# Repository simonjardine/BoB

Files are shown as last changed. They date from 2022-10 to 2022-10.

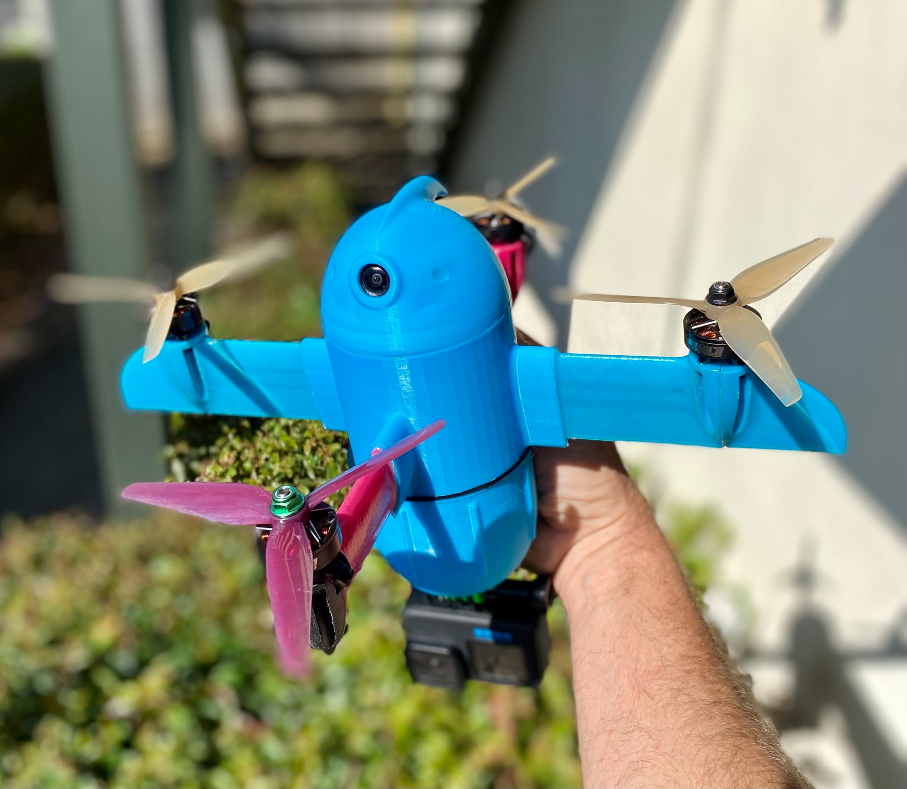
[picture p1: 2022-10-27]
bob.jpeg

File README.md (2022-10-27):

# BoB
Bob The Waterproof Drone
Hi, I'm BoB. I was born on the 10.10.2021 at 10.00am UTC

Simon Jardine is my maker, He built me and designed me to fly and even swim.
I'm called BoB because he said that I like to BoB, I also have a keel like a boat, so I always stay upright!!
Simon has been flying for 15 years, he thinks I'm the Worlds best Drone!!
So it must be true....

I am not the only waterproof Drone Simon has made, he made this one 10 years ago,
It was the very first waterproof Drone in The World.
https://www.youtube.com/watch?v=769Ppq-3Eaw&t=24s

How to build.. "BoB"

Apperently I'am a pleasure to build, everything slips in, wires will slide into the wings,
wings into fusealage, boom continues all the way to the motor mount.

You will need a 5mm boom to keep me rigid and strong for diving into the oceans.
The 5mm boom is a very tight fit, you will have to tap them carefully into the wings with a hammer, or sand them a little.
To keep me waterproof, use SikaSeal Aquarium Silicone Sealant, or something similar.
It's clear and easy to use, use a wet cloth to remove excess silicone.
Sand the parts first for a nice bond.

You'll also need superglue to connect my wing tips and motor mounts. Use medium CA and kicker for best adhesion!
There is a small hole in all of my motormounts, this was beacuse of my 5mm boom going all the way to my wingtips.
You will have to use silicone to fill these holes. 
Silicone also need to go into the wire section in the wings, both on the inside of the fusealage and end of wings.
Please don't super glue my Carbon boom, if you crash me, how will you repair me?

The STL files have 2 fuselage's, For a 20x20 FC and 30x30 FC.

The 30x30 fusealage also has another mounting hole for the Video Transmitter VTX, It was designed to use the TBS Transmitter.
Both holes use a 20x20 heatsink which are easyily purchased online.
Please note the larger ESC's will cope better with the heat and is highly recommended!!
The higher powered TX's also need a through hull fitting, becuase if I'm waterproof then things can get hot quickly.
It's also adviced to switch on temp within the OSD. You'll be able to keep an eye on my internal temperature.

Most importantly I fly as a PLUS not an X shape. So make sure in Betaflight to change me as a PLUS.
You will have to also adjust the YAW alignment. Make sure you check that I react correctly to your movements.

Enjoy BoB and please fly safely, Simon Jardine takes no responsibility for what you do with BoB.

HAPPY FLYING !!!!!!!!!!!

Simon and Bob :-)

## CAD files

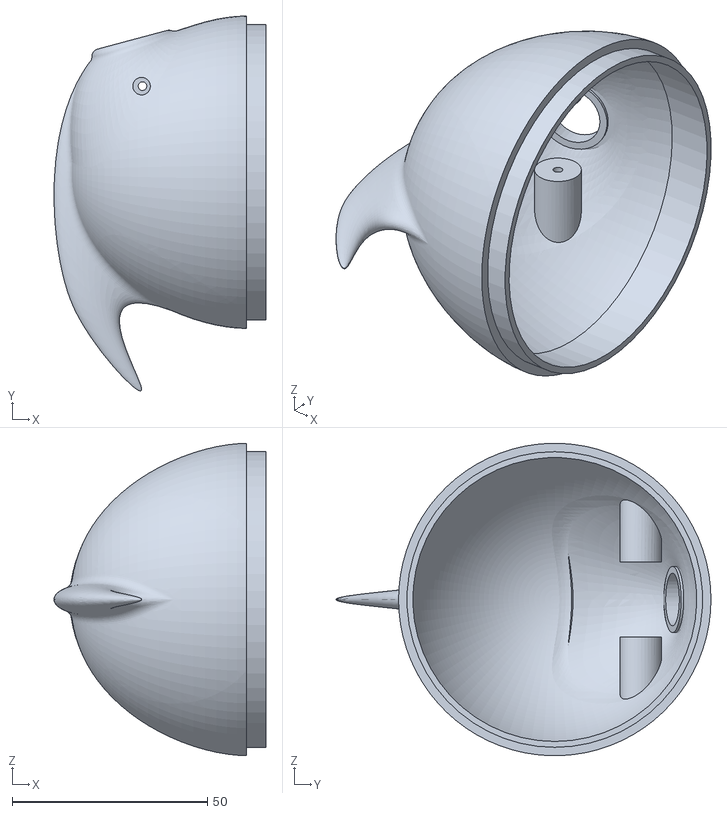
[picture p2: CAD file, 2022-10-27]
CanopyBottomparts/bobCanopy.STL
54.3 x 96.0 x 79.9

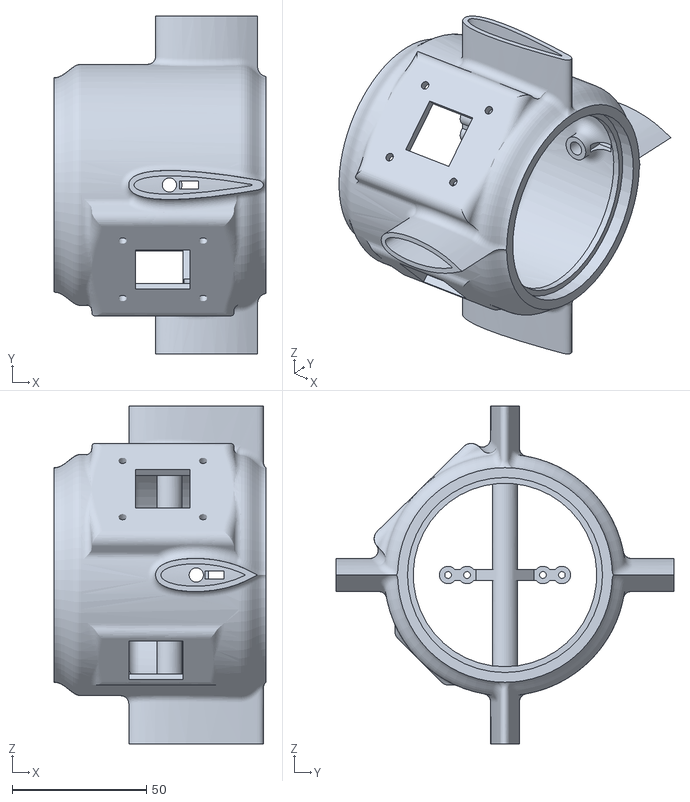
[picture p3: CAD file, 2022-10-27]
fuse30x30doubleheatsinks.STL
79.0 x 126.0 x 126.0

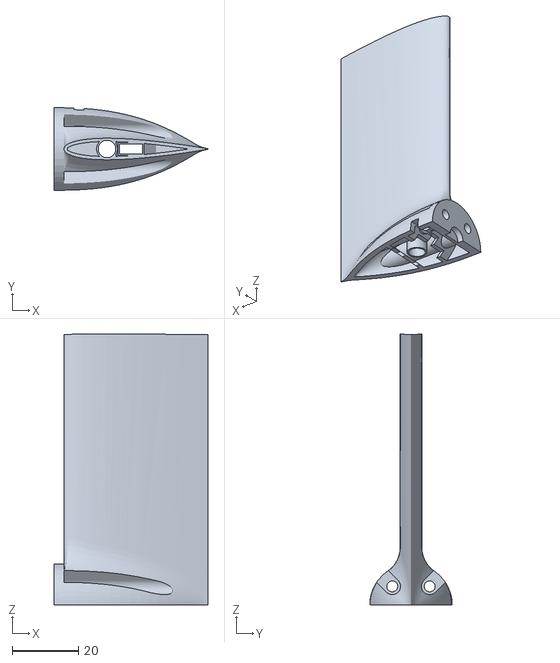
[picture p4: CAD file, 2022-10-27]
wingparts/leftwing.STL
46.6 x 25.0 x 82.1

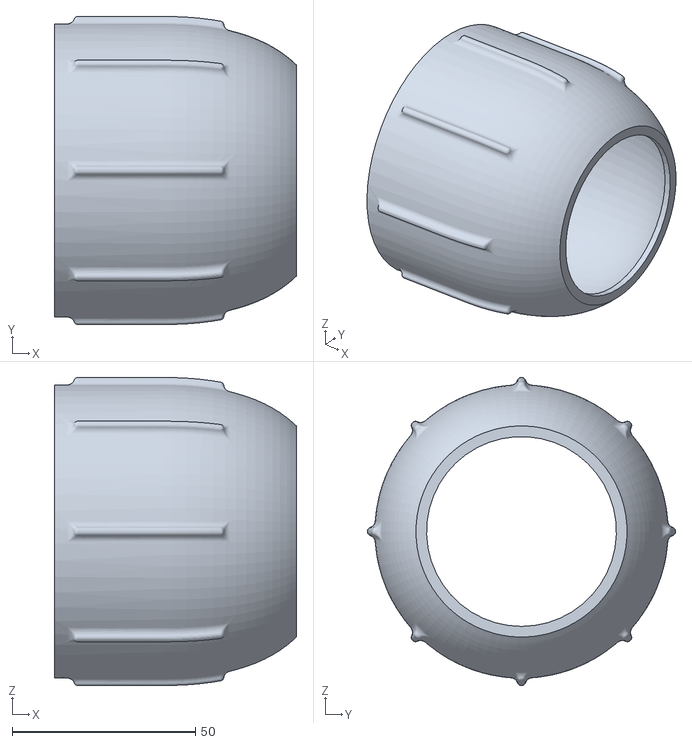
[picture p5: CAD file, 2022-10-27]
CanopyBottomparts/threadedbatteryholder.STL
66.0 x 84.0 x 84.0

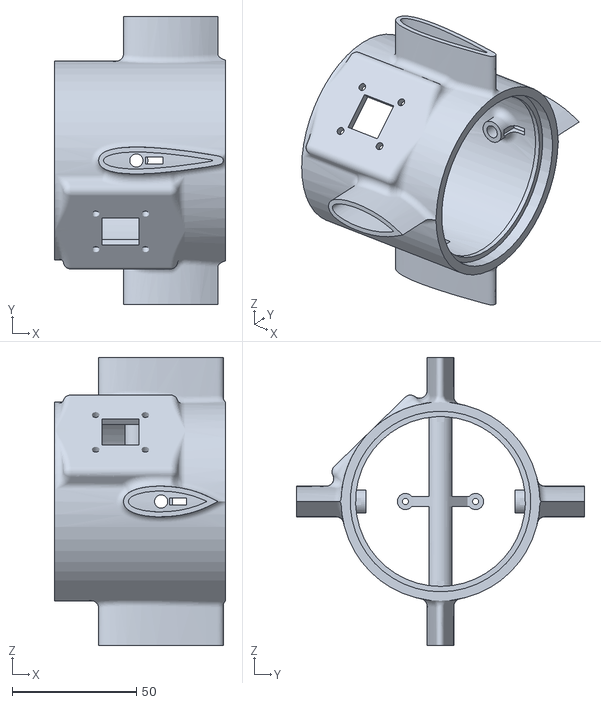
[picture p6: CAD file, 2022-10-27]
fuse20x20.STL
69.0 x 116.0 x 116.0

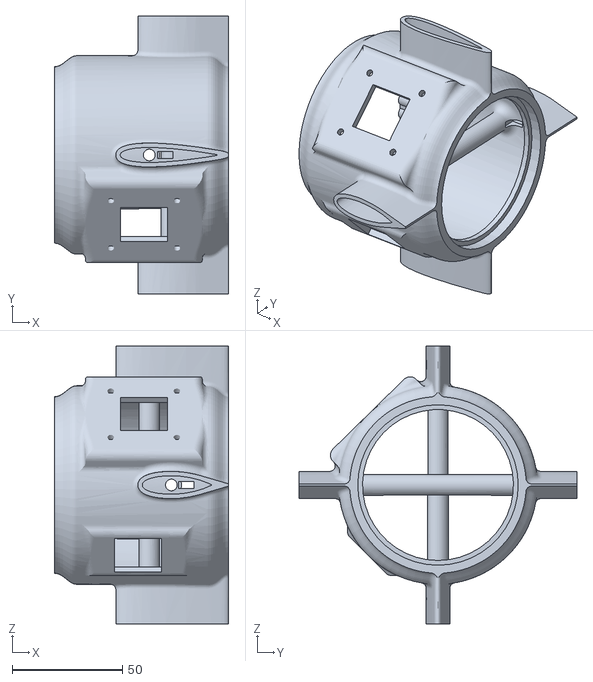
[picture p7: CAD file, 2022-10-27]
Mainfuselage/WP fuselage part2_2021.10.14.STL
79.0 x 126.0 x 126.0

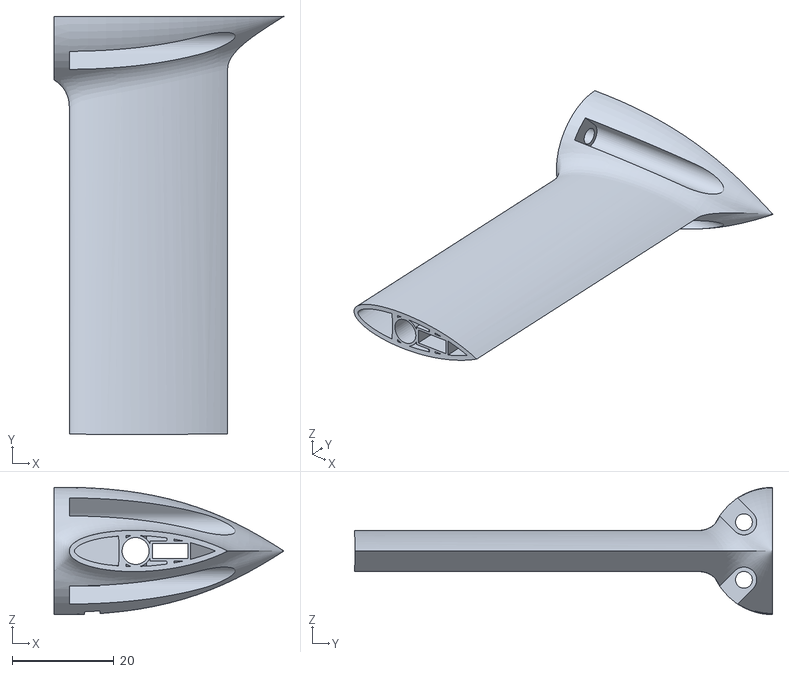
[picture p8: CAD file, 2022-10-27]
wingparts/bottomwing.STL
45.2 x 82.2 x 25.0

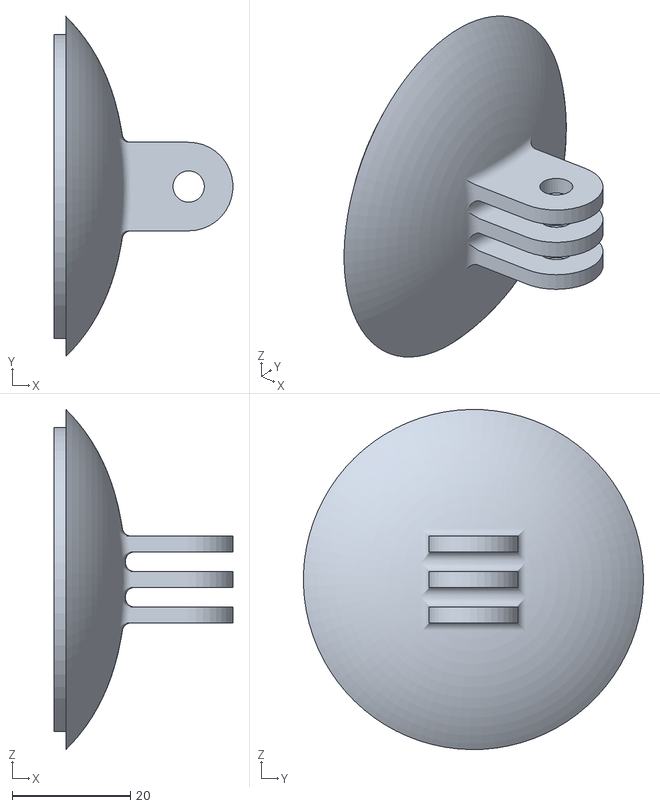
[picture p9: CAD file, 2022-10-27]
CanopyBottomparts/GoProbottom.STL
30.2 x 57.5 x 57.6

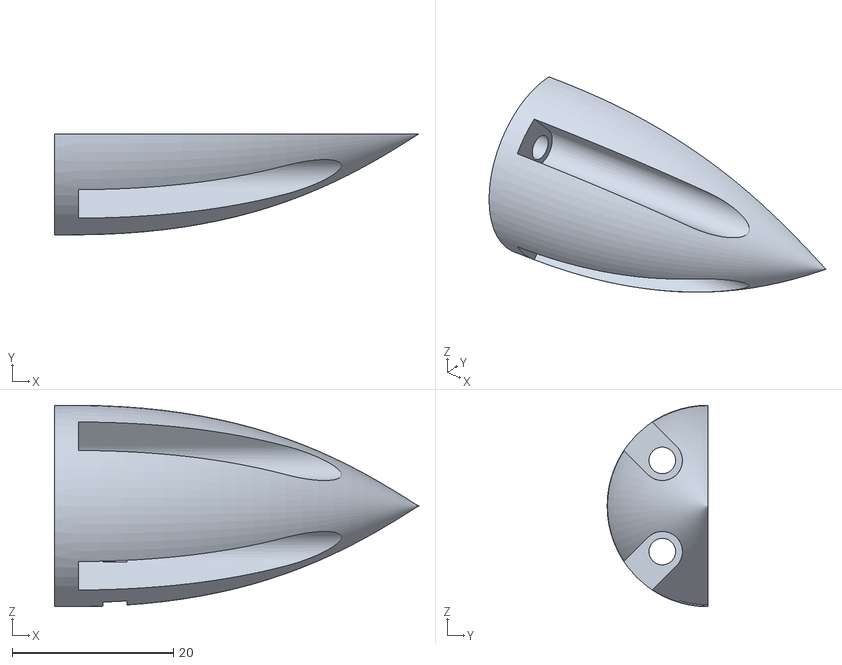
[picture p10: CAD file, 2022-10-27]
wingparts/topmotormount.STL
45.2 x 12.5 x 25.0

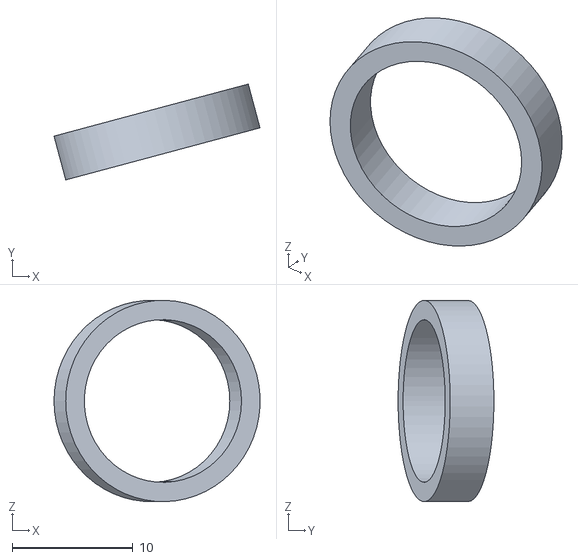
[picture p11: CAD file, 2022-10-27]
CanopyBottomparts/Ring for camera hole.STL
17.1 x 7.95 x 16.7

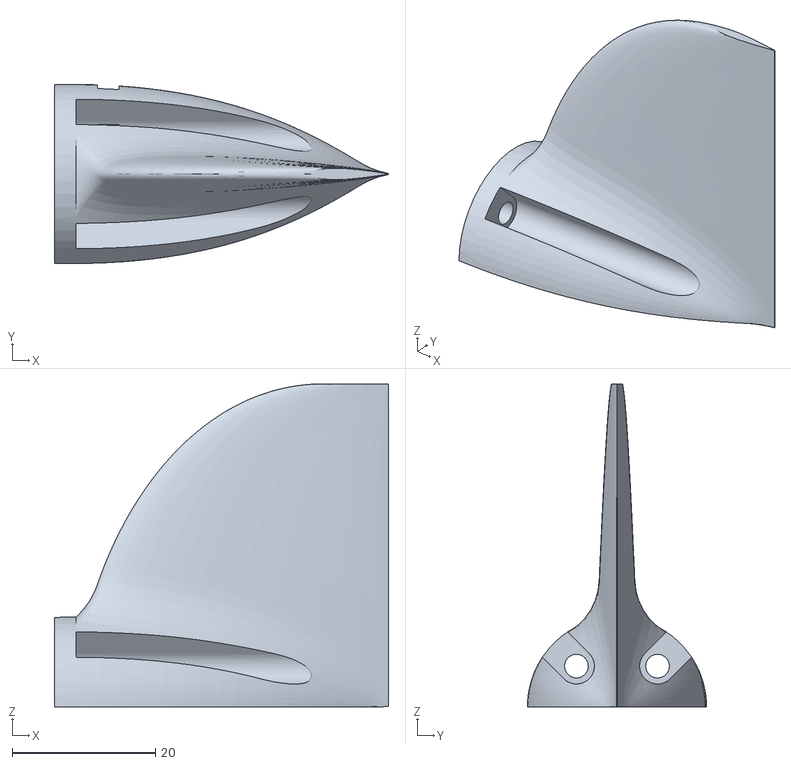
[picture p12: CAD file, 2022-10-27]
wingparts/rightwingtip.STL
46.6 x 25.0 x 45.0

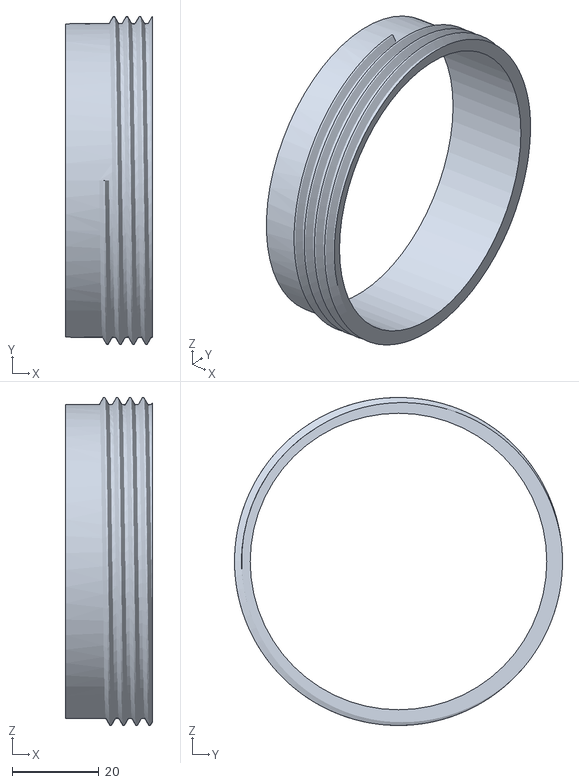
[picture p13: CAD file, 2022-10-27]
CanopyBottomparts/Lowerfusethread.STL
20.0 x 75.6 x 75.6

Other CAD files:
Mainfuselage/WP fuselage part2_larger ESC_with supports.STL
Mainfuselage/30x30fuselarger.STL
wingparts/rightwing.STL
wingparts/topwing.STL
wingparts/bottommotormount.STL
wingparts/leftwingtip.STL

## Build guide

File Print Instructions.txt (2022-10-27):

Printing....
I use an Ender 3 V2, but I also have the new FLsun Super Racer which is a Delta Printer (it's really amazing)

I am new to 3d Printing, so I won't be much use to you.
However these are the setting I used with great success.

I would use bright colours, Yellow, Orange, blue. 
I used PLA PLUS. You could also use any other materials, I've also used PLA/ 20%Carbon.
The GoPro mount must be printed in TPU slowly, (do not glue it until you have threaded the bottom on)
Or later when you go to use your GoPro it wil be facing a different direction, please take care doing this!!

I use CURA for slicing. 0.4 nozzle.
These are my settings for my Ender 3

Quality - Layer height 0.15
        - Line Width 0.4

Walls 5 (less is lighter and not as strong) (checked (outer walls before inner) (checked hide seam)
Top and bottom layers 4
Infill 0 
Material 225c and bed 55c
Speed 45mm/s 30 for inner and outer walls.
Travel retracion on
cooling on
Support is need only on the main fusealage and canopy my settings for support is.

Normal touching buildplate, 55 degrees support overhang.
(my printer didn't need(everywhere) only touching buildplate) (check this)
Lines (easy to remove)
15% support density
Support X/Y distance 0.7

Build plate Adhesion 8mm brim.
Surface mode is normal

*note
You can use Polyurethane (clear varnish with high UV)
Sand all the parts with 120 grit and varnish the parts, this will make it much more waterproof and keep the 
UV rays off your newly printed parts. I would persnally do this after BoB is built, becuase glue and silcone don't
like bonding to varnish.

I found with PLA + that going slowly and hotter 225C made the model very strong and much nice looking.

Good luck and enjoy BoB :-)

Simon
